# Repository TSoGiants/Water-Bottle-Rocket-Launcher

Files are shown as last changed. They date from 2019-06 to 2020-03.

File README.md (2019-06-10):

# About The Shoulders of Giants
In 1676, Isaac Newton, one of the most influential mathematicians and scientists of all time, famously wrote:

> "If I have seen further, it is by standing on the shoulders of giants."

The Shoulders of Giants, Inc. (TSoG) is a nonprofit (501(c)(3)) organization founded in 2013 on a vision that world-class science education should be available to all students of all ages. Since 2015, The Shoulders of Giants has offered an immersive, ongoing mentorship program for dedicated students who would like the opportunity to study more closely under the guidance of Dr. Steven J. Foland. This program is designed to provide middle and high school students with a broad foundation of knowledge and skills across science and engineering disciplines, experience working and communicating in a professional environment, and helps them develop the study habits necessary to achieve success at the university level and beyond.

In 2019, this world-class program became available to students everywhere with the launch of TSoG.tv. This online platform, created in collaboration between The Shoulders of Giants, Inc. and its sister-company Floating Point Laboratories, LLC, provides at-home exercises, live-streaming, and project support to students anywhere in the world.

## About Work in Progress
Work in Progress (WiP) is the main Kepler-level (high school) series on TSoG.tv, focused on multi-disciplinary engineering and applied science.

As the late, great astrophysicist and science advocate Carl Sagan once said: "If you wish to make an apple pie from scratch, you must first invent the universe." With that great quote in mind, this is a series where we bake the whole pie. In each season of Work in Progress we propose a practical project, lay out specifications, then discuss all of the relevant background knowledge necessary to take that project to completion.

Episodes of WiP air live on www.twitch.tv/tsogtv and are archived at www.youtube.com/tsogtv. This project is based on the work completed in episodes that aired on Monday evenings in Summer 2019.

# Water Bottle Rocket Launcher
## History and Motivation
We built our first water bottle rocket launcher in summer 2012 out of PVC pipe, zip ties, bits of string, and chewing gum. Based on one of many designs available online, our original model was ugly and unreliable.

In 2013, a team of TSoG volunteers created a minor redesign that incorporated a bike handle brake mechanism to enable users to trigger a launch from a safe distance outside the "splash zone" of the launcher. This, along with a few other small quality-of-life improvements, made for a much more reliable launch platform. The three copies that we built using this design were used in a variety of outreach activities for elementary students for the next 5 years.

In May 2019, TSoG co-founder Steven J. Foland proposed an updated redesign of this part of TSoG history could serve as one of the first seasons of the new series, Work in Progress. Now with years of water bottle rocket experience behind him and the vast improvements in rapid prototyping that the 3D printing revolution has enabled, Dr. Foland was confident that he and his students could work together to produce the ultimate launcher. 

## Current State
As the name of the series implies, this redesign is currently a work in progress. This section of the README will be kept up-to-date with the current state of the project as the season progresses.

### Design Inputs
* Must fit a variety of soda bottle brands and sizes ranging from 16 oz to 2 liter.
* Must be able to be operated solo: Able to turn the launcher upside down easily for loading *and* able to retract the cuff and load a liquid-filled bottle.
* Must be able to adjust launch angle to account for hills.
* Must be able to trigger launch remotely.

### Old Design Fixes
There are a numer of improvements that should be made to the old design which, while not necessarily distinct design inputs, would make replication, reliability, and usability significantly better than the old model.
* Should fold down for easy portability.
* Must be comprised entirely of either: Standard, off-the-shelf parts, *or* 3D printed components.
* All components which must hold pressure should be comprised of standard PVC fittings (NO janky welds or epoxy fixes).
* No exposed sharp edges!

### How to Collaborate
For any active TSoG.tv students who would like to contribute to this project, please create a GitHub account and contact Dr. Foland via Discord. He will need your GitHub username to grant you permission to modify this repository.

This is a primarily mechanical CAD focused project that we will be completing in Alibre Design. You can download a 30 day trial of this software [here](https://www.alibre.com/get-a-trial-of-alibre-design-expert/). Students active on this project should discuss longer-term licensing options with Dr. Foland.

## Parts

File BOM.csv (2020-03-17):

Description | Part Number | Manufacturer | Distributor | Link | Unit Cost | Quantity | Total Cost | Notes
Schrader Valve to 1/8" NPT | 684 | Milton | Amazon | https://www.amazon.com/Milton-684-NPT-Tank-Valve/dp/B001O2ZL5C | $1.65 | 1 | $1.65 | Minimum quantity is 10 valves at this price.
ASME-Code Fast-Acting Pressure-Relief Valve (100 PSI) | 48435K71 |  | McMaster-Carr | https://www.mcmaster.com/48435k71-48435K713 | $5.62 | 1 | $5.62
6' Compressor Air Extension Hose | 16 | VIAIR | Amazon | https://www.amazon.com/VIAIR-00016-Portable-Compressor-Extension/dp/B00ELJD0BW | $5.60 | 1 | $5.60
Sch. 40 PVC 1/2" Socket Male x 1/8" NPT Female Bushing | 4880K821 |  | McMaster-Carr | https://www.mcmaster.com/4880k821 | $0.67 | 2 | $1.34
Sch. 40 PVC 1/2" T Connect Female | 4880k41 |  | McMaster-Carr | https://www.mcmaster.com/4880k41 | $0.38 | 1 | $0.38
Sch. 40 PVC 1/2" Conduit, 10ft | 72808 | JM Eagle | Lowes | https://www.lowes.com/pd/JM-Eagle-Common-1-2-in-Actual-0-62-In-Non-Metallic-Pvc-10-ft-Conduit/3129569 | $2.16 | 1 | $2.16
Brake cable housing | N/A |  | Amazon | https://www.amazon.com/Pyramid-Lined-Cable-Housing-Roll/dp/B002G3BJG8 | $0.98 | 2.5 | $2.45 | Unit cost is per meter. Minimum quantity is 15.24m (50 ft) @ $16.01
Stainless steel wire rope, 1/16" | KEROMER-001 | KEROMER | Amazon | https://www.amazon.com/Stainless-Strand-inches-Breaking-Strength/dp/B07LBK24TG | $0.27 | 3 | $0.81 | Unit cost is per meter. Minimum quantity is 100m (328 ft) @ $29.99.
Brake cable ferrule | N/A | KEROMER | Amazon | N/A | $0.00 | 2 | $0.00 | Ferrules are included with the KEROMER stainless steel cable.
Music Wire Steel Extension Spring - 2.25" Long | 9044K371 |  | McMaster-Carr | https://www.mcmaster.com/9044k371 | $2.24 | 1 | $2.24 | Unit cost is per spring. Min quantity is 3 @ $6.74.
302 Stainless Steel Compression Spring - 1.25" Long | 1986K69 |  | McMaster-Carr | https://www.mcmaster.com/1986k69 | $0.55 | 2 | $1.11 | Unit cost is per spring. Min quantity is 6 @ $3.32.
302 Stainless Steel Compression Spring - 2" Long | 1986K82 |  | McMaster-Carr | https://www.mcmaster.com/1986k82 | $0.57 | 1 | $0.57 | Unit cost is per spring. Min quantity is 6 @ $3.41.
11" Cable Ties | 1295732 | Utilitech | Lowes | https://www.lowes.com/pd/Utilitech-500-Pack-11-in-Cable-Ties/999971170 | $0.06 | 8 | $0.48 | Unit cost is per zip tie. Price is significantly lower if purchased in large volume.
#8 x 1/2" Extra-Wide Rounded Head Drilling Screws | 91515A100 |  | McMaster-Carr | https://www.mcmaster.com/91515a100 | $0.05 | 20 | $1.00 | Unit cost is per screw. Min quantity is 100 at $4.83.
#4 x 1/2" Philips Rounded Head Screws for Sheet Metal | 90190A110 |  | McMaster-Carr | https://www.mcmaster.com/90190a110 | $0.03 | 11 | $0.33 | Unit cost is per screw. Min quantity is 100 at $2.68
#4 x 3/4" Philips Rounded Head Screws for Sheet Metal | 90190A113 |  | McMaster-Carr | https://www.mcmaster.com/90190a113 | $0.03 | 2 | $0.06 | Unit cost is per screw. Min quantity is 100 at $2.94
 |  |  |  |  |  |  |  | Cost for all printed parts is based on a $22 / kg for plastic.
Base Cap |  |  |  |  | $1.10 | 2 | $2.21 | 0.0502 | kg
Cross Brace |  |  |  |  | $1.45 | 1 | $1.45 | 0.0657 | kg
Hinge 1 |  |  |  |  | $0.90 | 2 | $1.80 | 0.0408 | kg
Hinge 2 |  |  |  |  | $1.00 | 2 | $2.00 | 0.0454 | kg
Hinge Knob |  |  |  |  | $0.66 | 2 | $1.31 | 0.0298 | kg
Plate Knob |  |  |  |  | $0.37 | 1 | $0.37 | 0.0167 | kg
Plate Threaded |  |  |  |  | $2.44 | 1 | $2.44 | 0.1107 | kg
Plate Threaded Endcap |  |  |  |  | $0.21 | 1 | $0.21 | 0.0097 | kg
Plate Unthreaded |  |  |  |  | $2.74 | 1 | $2.74 | 0.1247 | kg
Cable Housing Clamp |  |  |  |  | $0.13 | 1 | $0.13 | 0.0058 | kg
Cuff |  |  |  |  | $2.07 | 1 | $2.07 | 0.0942 | kg
Cuff Cover |  |  |  |  | $0.68 | 1 | $0.68 | 0.0307 | kg
Threaded Inner |  |  |  |  | $1.09 | 1 | $1.09 | 0.0495 | kg
Threaded Outer |  |  |  |  | $2.22 | 1 | $2.22 | 0.1011 | kg
Button Slide |  |  |  |  | $0.28 | 1 | $0.28 | 0.0129 | kg
Button Top |  |  |  |  | $0.28 | 1 | $0.28 | 0.0127 | kg
Housing Bottom |  |  |  |  | $1.42 | 1 | $1.42 | 0.0645 | kg
Housing Top |  |  |  |  | $1.40 | 1 | $1.40 | 0.0638 | kg
Sled |  |  |  |  | $0.38 | 1 | $0.38 | 0.0174 | kg
 |  |  |  |  | Total |  | $50.28

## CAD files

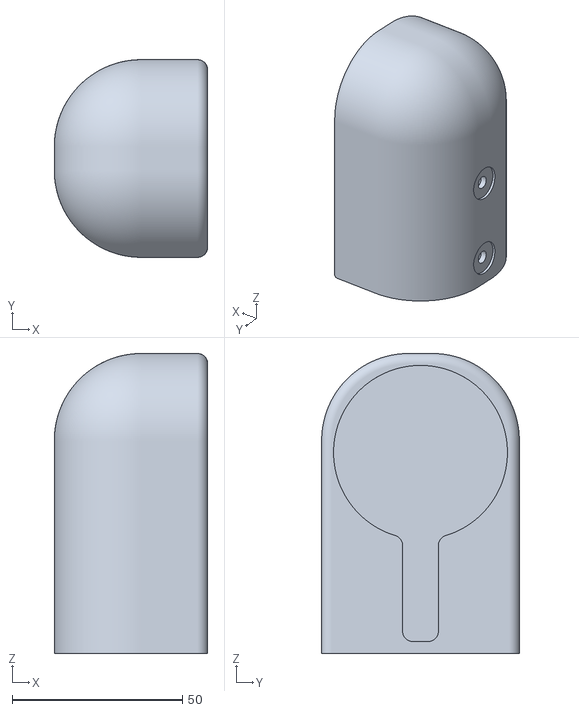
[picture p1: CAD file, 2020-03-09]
CAM/Base/STL/Base_Cap.stl
45.0 x 58.0 x 88.0

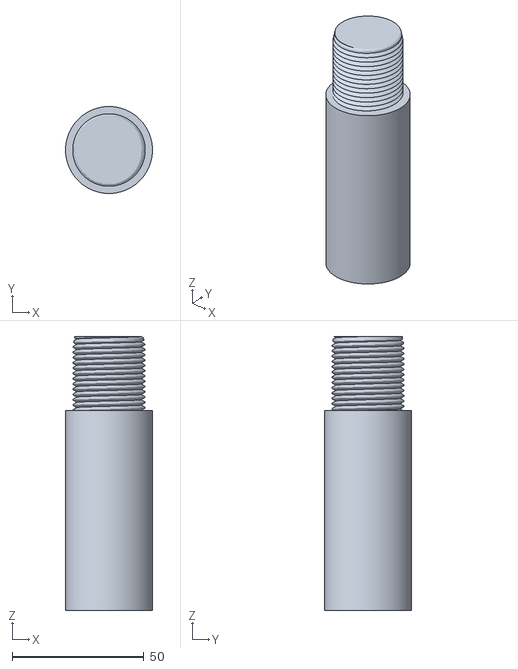
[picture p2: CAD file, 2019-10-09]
CAM/Jigs/STL/Zip_Tie_Jig.stl
33.0 x 33.0 x 104.0

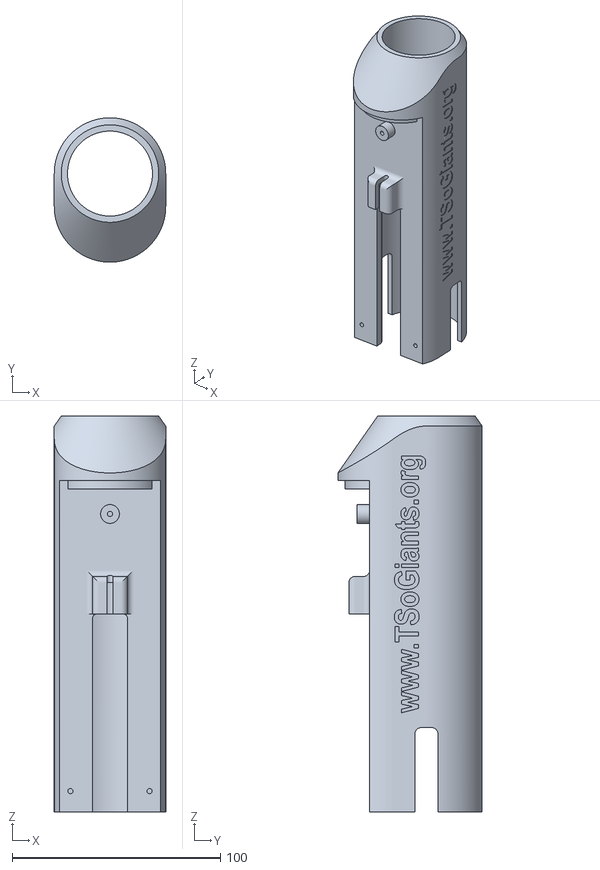
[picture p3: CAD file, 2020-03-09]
CAM/Nozzle/STL/Cuff.stl
53.5 x 69.2 x 190.0

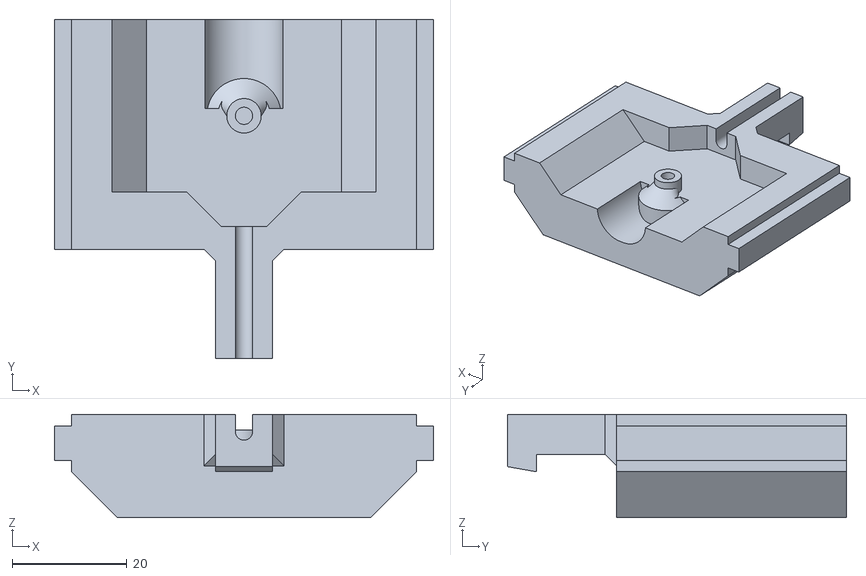
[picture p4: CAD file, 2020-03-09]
CAM/Trigger/STL/Sled.stl
66.0 x 59.0 x 18.0

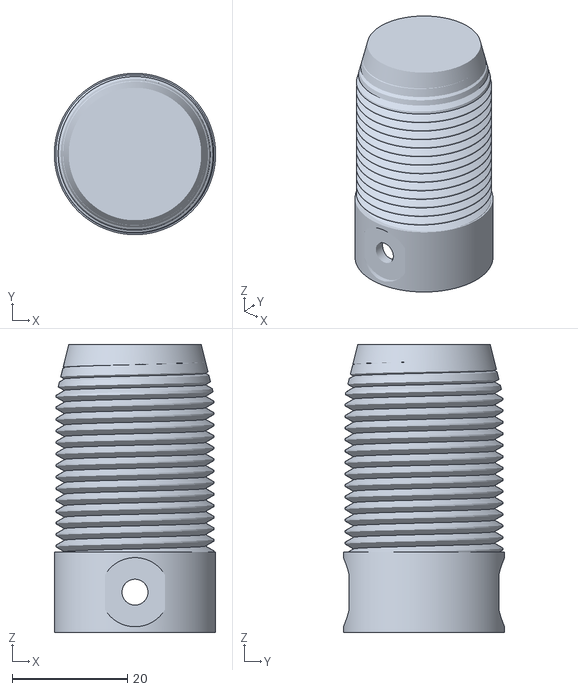
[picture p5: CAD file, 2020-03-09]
CAM/Base/STL/Plate_Threaded_Endcap.stl
28.0 x 28.0 x 50.0

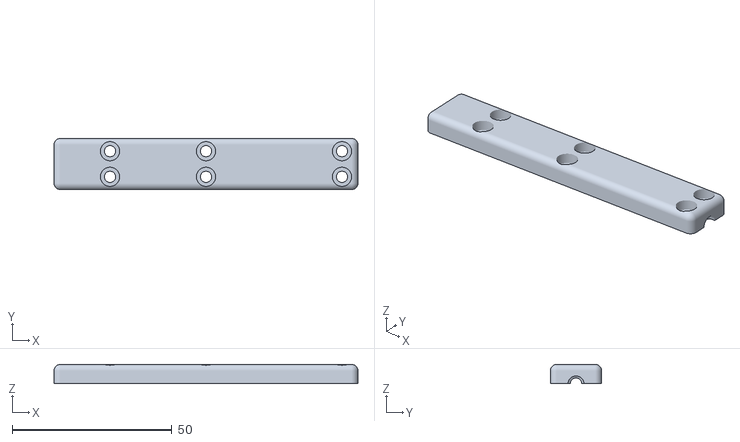
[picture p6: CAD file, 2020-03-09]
CAM/Nozzle/STL/Cable_Housing_clamp.stl
95.0 x 16.0 x 6.00

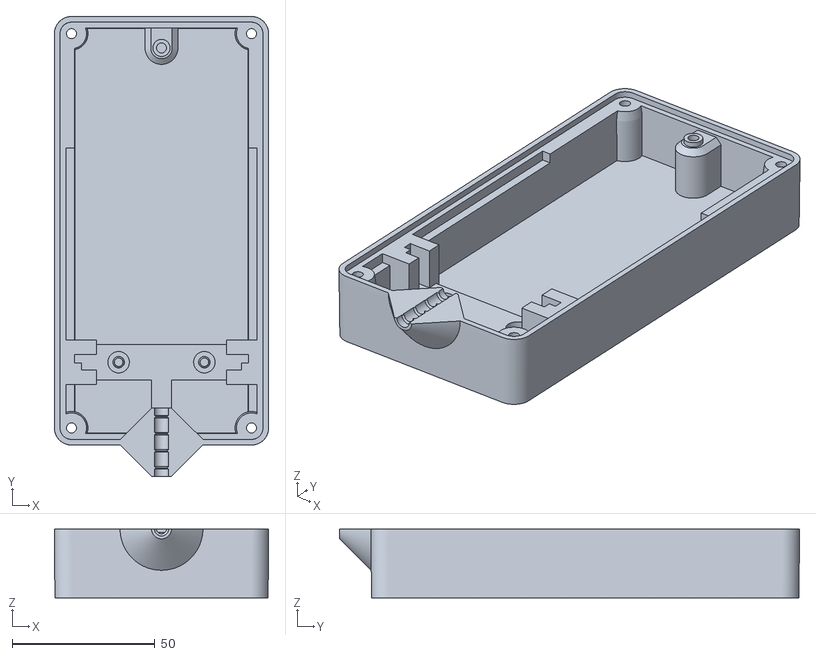
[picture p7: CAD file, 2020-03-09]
CAM/Trigger/STL/Housing_Bottom.stl
75.0 x 161.0 x 24.0

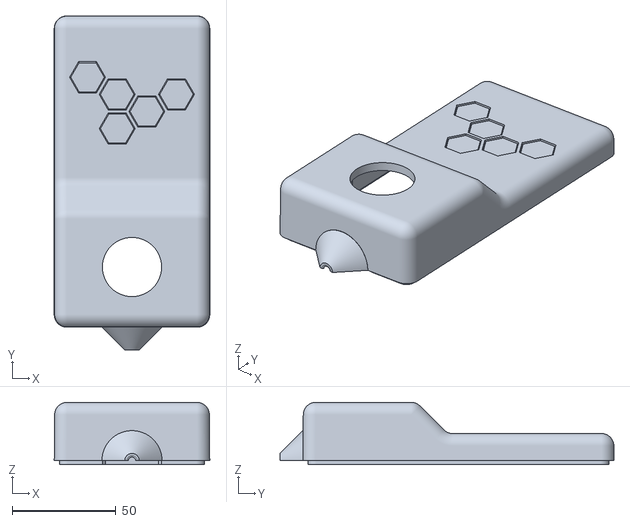
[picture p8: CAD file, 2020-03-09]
CAM/Trigger/STL/Housing_Top.stl
75.0 x 161.0 x 30.0

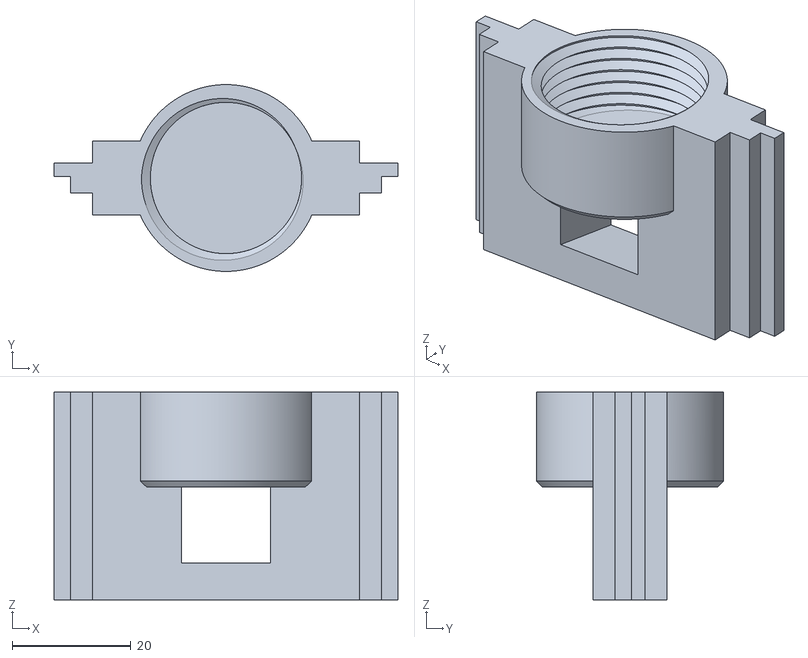
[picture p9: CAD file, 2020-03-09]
CAM/Trigger/STL/Button_slide.stl
58.0 x 31.5 x 35.0

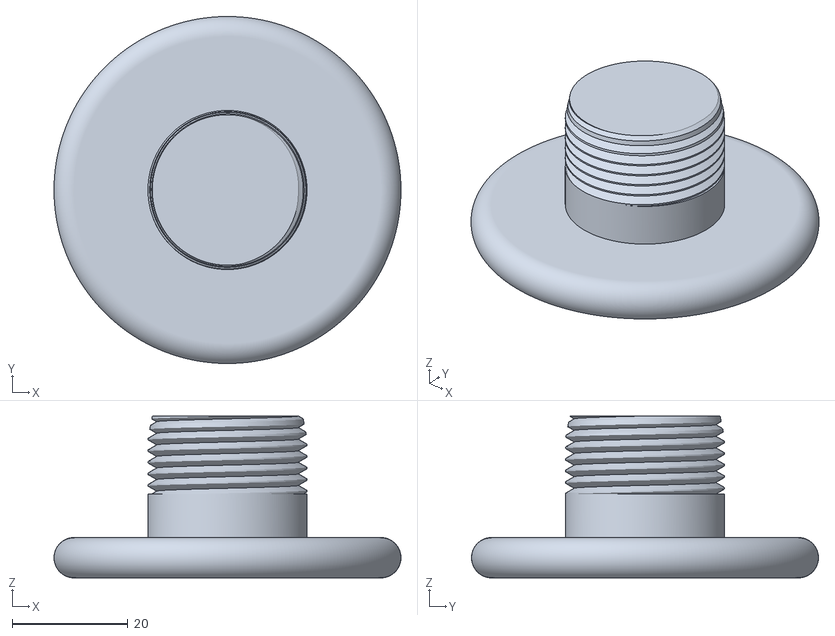
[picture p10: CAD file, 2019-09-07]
CAM/Trigger/STL/Button_top.stl
60.0 x 60.0 x 28.0

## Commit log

2019-06-10 Created BOM as .csv file.
    [BOM.csv]
2019-06-11 Rearranged CAD file structure
    Modelled a few new parts and reorganized the CAD folder.
2019-06-11 Fixed assembly reference problem.
2019-06-18 Modified the Zip Tie Holder on Threaded Outer
2019-06-24 Preparations made for WiP E03.
    [Cuff.stl]
2019-07-02 End of episode 04 - updated threaded outer.
2019-07-13 End of Episode 05
    Added slot on cuff and threaded inner for brake cable assembly / fixed tolerances on threaded inner.
2019-07-29 Updated assembly colors.
2019-07-30 End of episode 06.
    [Cuff.stl]
2019-07-30 Made a few small changes prior to printing.
2019-08-05 Added Trigger mechanism designs
    This is an implementation of a Nerf-gun style trigger mechanism for the launcher.
    These designs are in a assembly, and the parts move as they should in real life.
2019-08-06 Fixed threaded tolerances
    Also increased space around screwholes on threaded outer.
2019-08-06 End of episode 7
    [Cuff.stl]
2019-08-06 Made a few minor post-episode-7 modifications to clean up the Housing_bottom part.
2019-08-06 Created a new trigger and sled design. Tested the parts in a new assembly. Moved former trigger/mission control parts to a folder within "parts to print" folder.
2019-08-09 Added tracks for the trigger-hook to move. Re-did mates and alignments for mission control assembly
2019-08-13 Completed flange-cuff assembly.
2019-08-19 End of Episode 08.
    [Cable_Housing_Spacer.stl, Cable_Housing_clamp.stl, Cable_washer.stl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]
2019-09-03 Completed first draft of button mechanism.
2019-09-07 Modified mission control housing for printing.
    [Button_slide.stl, Button_top.stl, Housing_Bottom.stl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]
2019-09-10 Pre-Episode 12 commit.
    [Housing_Bottom.stl, Housing_Top.stl, Sled.stl]
2019-09-10 Keyed button slide and track.
2019-09-10 End of Episode 12 commit.
    [CrossBrace.stl]
2019-10-09 End of episode 13.
    [Button_slide.stl, Button_top.stl, Cable_Housing_Spacer.stl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]
2019-12-13 Fixed a few minor issues.
    [Cable_Housing_Spacer.stl, Cable_Housing_clamp.stl, Cuff_tip.stl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]
2020-02-28 Pre-GSNETX modificaitions to trigger mechanism.
    [Button_slide.stl, Housing_Bottom.stl, Housing_Top.stl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]
2020-03-04 Updated BOM
    [BOM.csv]
2020-03-08 End of 2020 encore revisions.
    [BOM.csv]
2020-03-09 Post-encore episode cleanup.
    [BOM.csv, Base_Cap.stl, Button_slide.stl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]
